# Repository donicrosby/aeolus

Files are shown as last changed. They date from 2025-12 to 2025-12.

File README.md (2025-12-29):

# Aeolus
A modular window extraction fan that uses common PC fans as the extraction component

## Setup
There are a few submodules that need to be pulled in this can be done by:

```bash
git clone --recurse-submodules https://github.com/donicrosby/aeolus.git
```

Or after already cloning the repo:

```bash
git clone ttps://github.com/donicrosby/aeolus.git
git submodule update --init --recursive
```

## Notes
This is a Kicad 9 project, ensure that you use that version when viewing

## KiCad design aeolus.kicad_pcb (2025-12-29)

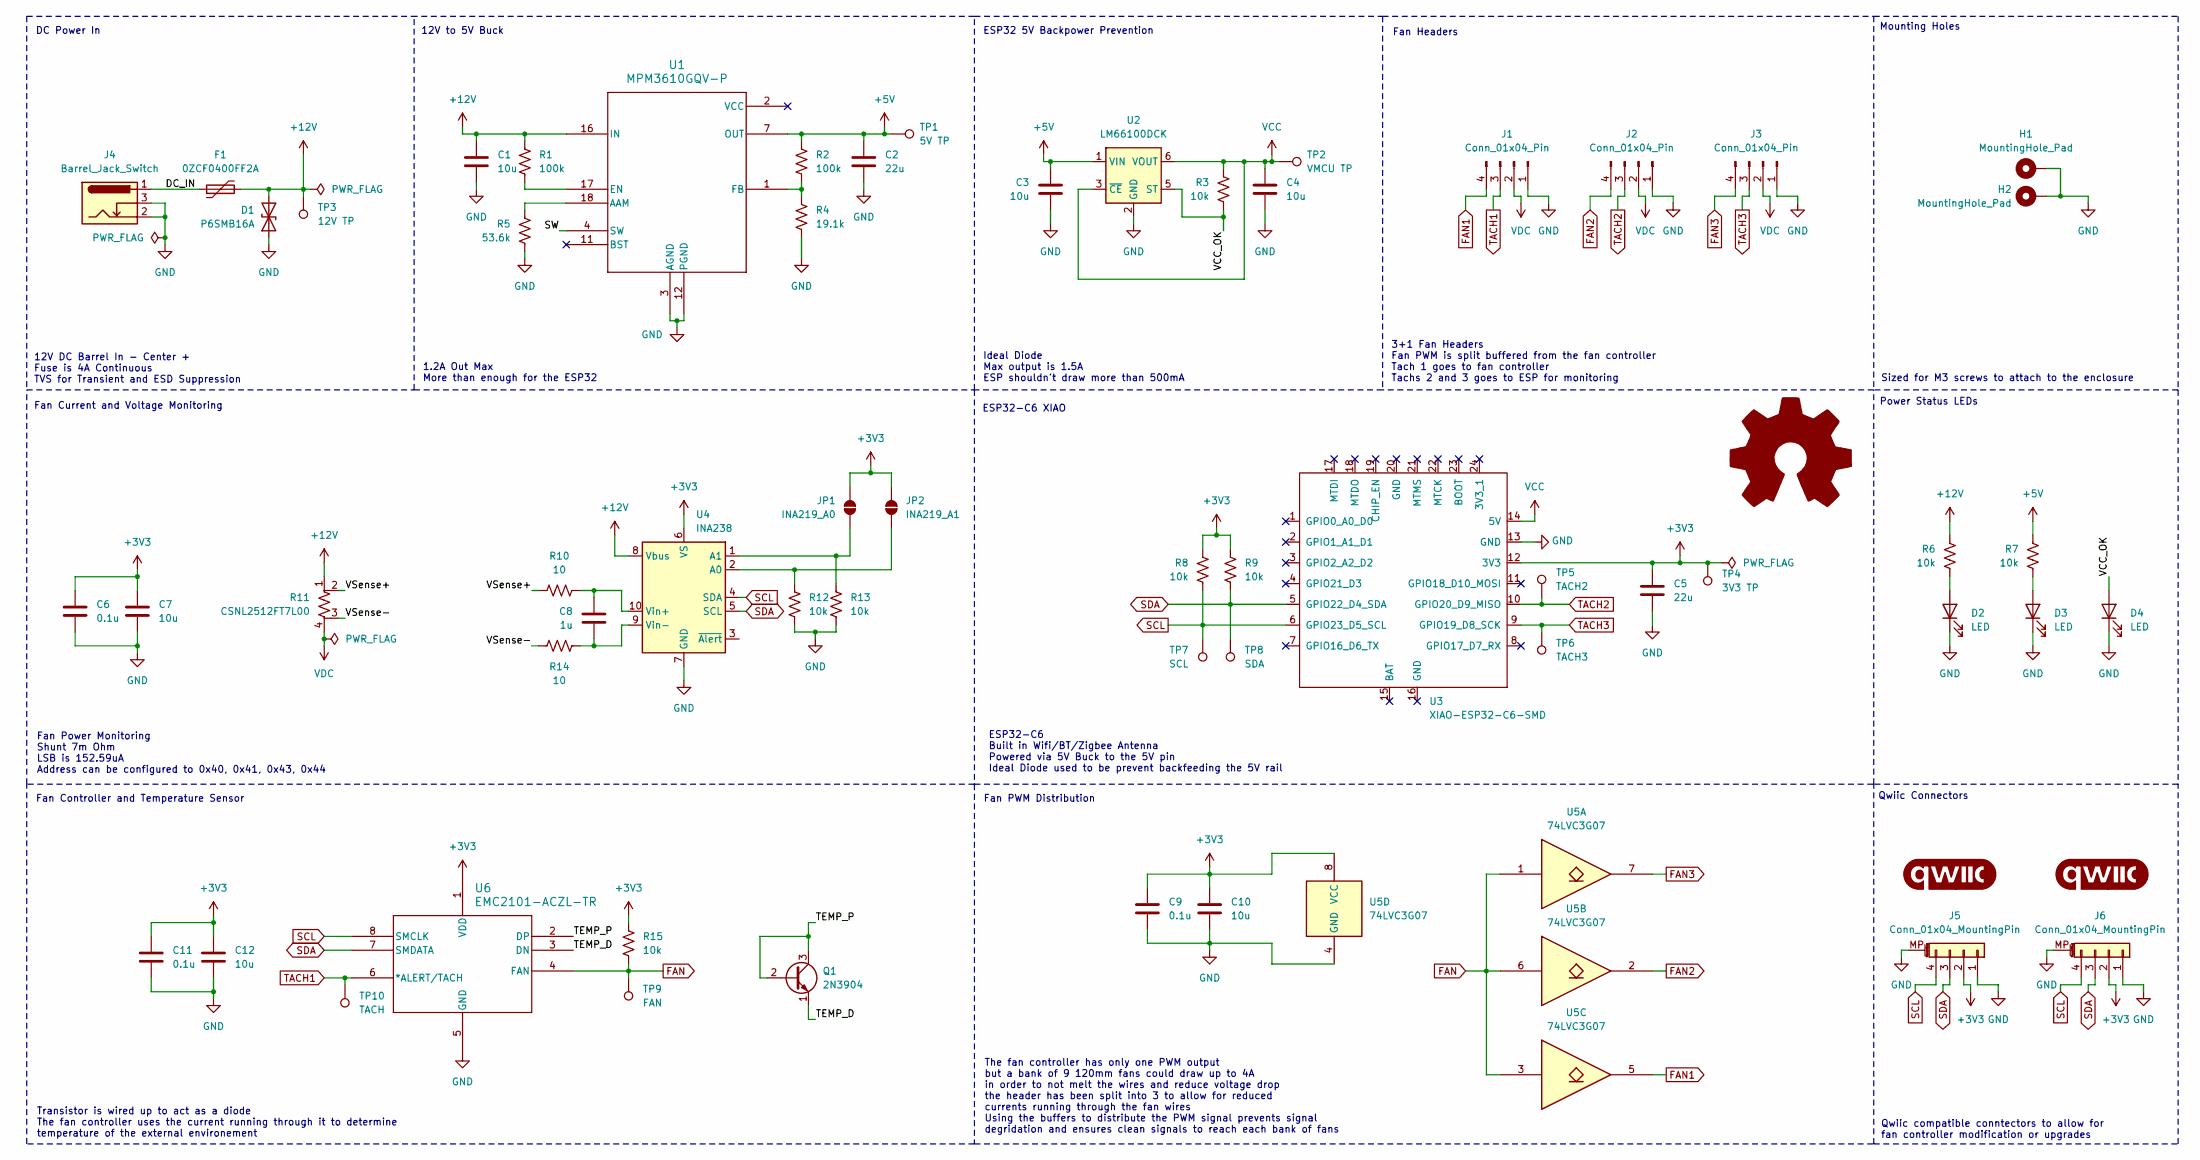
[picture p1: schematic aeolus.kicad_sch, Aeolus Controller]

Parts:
C1, C3, C4, C7, C10, C12: 10u; C_0805_2012Metric; MPN CL21A106KAYNNNE; LCSC C15850
C2, C5: 22u; C_0805_2012Metric; MPN CL21A226MAYNNNE; LCSC C602037
C6, C9, C11: 0.1u; C_0805_2012Metric; MPN CL21B104KBCNNNC; LCSC C5137467
C8: 1u; C_0805_2012Metric_Pad1.18x1.45mm_HandSolder; MPN CL21B105KBFNNNE; LCSC C5137467
D1: P6SMB16A; D_SMB; MPN P6SMB16A; LCSC C286252
D2: LED; LED_1206_3216Metric; MPN LTST-C150KSKT; LCSC C2985981
D3: LED; LED_1206_3216Metric; MPN LTST-C150KRKT; LCSC C2984265
D4: LED; LED_1206_3216Metric; MPN LTST-C150KGKT; LCSC C2984261
F1: 0ZCF0400FF2A; Fuse_2920_7451Metric; MPN 0ZCF0400FF2A
G1, G2: qwiic_Logo; qwiic_5.5mm
H1, H2: MountingHole_Pad; MountingHole_3.2mm_M3_Pad_Via
J1, J2, J3: Conn_01x04_Pin; FanPinHeader_1x04_P2.54mm_Vertical; MPN 470531000
J4: Barrel_Jack_Switch; BarrelJack_Wuerth_6941xx301002; MPN PJ-002AH
J5, J6: Conn_01x04_MountingPin; JST BM04B-SRSS-TB(LF)(SN)_4xP1.00mm; MPN BM04B-SRSS-TB(LF)(SN)
JP1: INA219_A0; SolderJumper-2_P1.3mm_Open_TrianglePad1.0x1.5mm
JP2: INA219_A1; SolderJumper-2_P1.3mm_Open_TrianglePad1.0x1.5mm
Q1: 2N3904; TO-92_Inline; MPN 2N3904
R1, R2: 100k; R_0805_2012Metric; MPN RC0805FR-07100KL; LCSC C96346
R3, R6, R7, R8, R9, R12, R13, R15: 10k; R_0805_2012Metric; MPN CRCW080510K0FKEAC; LCSC C84376
R4: 19.1k; R_0805_2012Metric; MPN RC0805FR-0719K1L; LCSC C2930175
R5: 53.6k; R_0805_2012Metric; MPN RC0805FR-0753K6L; LCSC C5153984
R10, R14: 10; R_0805_2012Metric_Pad1.20x1.40mm_HandSolder; MPN RM10J000CT; LCSC C17477
R11: CSNL2512FT7L00; Stackpole_Shunt_2512_Kelvin_7mOhm; MPN CMS-R050-1.0; LCSC C500733
TP1: 5V TP; TestPoint_Pad_D2.0mm
TP2: VMCU TP; TestPoint_Pad_D2.0mm
TP3: 12V TP; TestPoint_Pad_D2.0mm
TP4: 3V3 TP; TestPoint_Pad_D2.0mm
TP5: TACH2; TestPoint_Pad_D2.0mm
TP6: TACH3; TestPoint_Pad_D2.0mm
TP7: SCL; TestPoint_Pad_D2.0mm
TP8: SDA; TestPoint_Pad_D2.0mm
TP9: FAN; TestPoint_Pad_D2.0mm
TP10: TACH; TestPoint_Pad_D2.0mm
U1: MPM3610GQV-P; QFN3p0x5p0x1p6_MPM3610_MNP; MPN MPM3610GQV-P; LCSC C5183856
U2: LM66100DCK; SOT-363_SC-70-6; MPN LM66100DCKR; LCSC C2832141
U3: XIAO-ESP32-C6-SMD; XIAO-ESP32C6-SMD; MPN 113991254; LCSC C9900124963
U4: INA238; VSSOP-10_3x3mm_P0.5mm
U5: 74LVC3G07; SSOP-8_2.95x2.8mm_P0.65mm; MPN 74LVC3G07SS8-7; LCSC C2871847
U6: EMC2101-ACZL-TR; MSOP-8_3x3mm_P0.65mm; MPN EMC2101-ACZL-TR; LCSC C626967

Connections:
+3V3: C5.1, C6.1, C7.1, C9.1, C10.1, C11.1, C12.1, J5.2, J6.2, JP1.2 (B), JP2.2 (B), R8.1, R9.1, R15.1, TP4.1, U3.12 (3V3), U4.6 (VS), U5.8 (VCC), U6.1 (VDD)
+5V: C2.1, C3.1, R2.1, R7.1, TP1.1, U1.7 (OUT), U1.8 (OUT), U1.9 (OUT), U2.1 (VIN)
+12V: C1.1, D1.2 (A2), F1.2, R1.1, R6.1, R11.1, TP3.1, U1.16 (IN), U4.8 (Vbus)
/DC_IN: F1.1, J4.1
/SW: U1.4 (SW), U1.5 (SW), U1.6 (SW)
/TEMP_D: Q1.1 (E), U6.3 (DN)
/TEMP_P: Q1.2 (B), Q1.3 (C), U6.2 (DP)
/VCC_OK: D4.2 (A), R3.2, U2.5 (ST)
/VSense+: R10.1, R11.2
/VSense-: R11.3, R14.1
FAN: R15.2, TP9.1, U5.1, U5.3, U5.6, U6.4 (FAN)
FAN1: J1.4, U5.5
FAN2: J2.4, U5.2
FAN3: J3.4, U5.7
GND: C1.2, C2.2, C3.2, C4.2, C5.2, C6.2, C7.2, C9.2, C10.2, C11.2, C12.2, D1.1 (A1), D2.1 (K), D3.1 (K), D4.1 (K), H1.1, H2.1, J1.1, J2.1, J3.1, J4.2, J4.3, J5.1, J5.MP (MountPin), J6.1, J6.MP (MountPin), R4.2, R5.2, R12.2, R13.2, U1.3 (AGND), U1.12 (PGND), U1.13 (PGND), U1.14 (PGND), U2.2 (GND), U3.13 (GND), U4.7 (GND), U5.4 (GND), U6.5 (GND)
unnamed: D2.2 (A), R6.2
unnamed: D3.2 (A), R7.2
unnamed: JP1.1 (A), R13.1, U4.1 (A1)
unnamed: JP2.1 (A), R12.1, U4.2 (A0)
unnamed: R5.1, U1.18 (AAM)
unnamed: R1.2, U1.17 (EN)
unnamed: R2.2, R4.1, U1.1 (FB)
unnamed: C8.1, R10.2, U4.10 (Vin+)
unnamed: C8.2, R14.2, U4.9 (Vin-)
SCL: J5.4, J6.4, R8.2, TP7.1, U3.6 (GPIO23_D5_SCL), U4.4 (SDA), U6.8 (SMCLK)
SDA: J5.3, J6.3, R9.2, TP8.1, U3.5 (GPIO22_D4_SDA), U4.5 (SCL), U6.7 (SMDATA)
TACH1: J1.3, TP10.1, U6.6 (*ALERT/TACH)
TACH2: J2.3, TP5.1, U3.10 (GPIO20_D9_MISO)
TACH3: J3.3, TP6.1, U3.9 (GPIO19_D8_SCK)
VCC: C4.1, R3.1, TP2.1, U2.3 (~CE), U2.6 (VOUT), U3.14 (5V)
VDC: J1.2, J2.2, J3.2, R11.4

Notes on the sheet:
Fan Headers
Transistor is wired up to act as a diode The fan controller uses the current running through it to determine temperature of the external environement
ESP32 5V Backpower Prevention
12V to 5V Buck
3+1 Fan Headers Fan PWM is split buffered from the fan controller Tach 1 goes to fan controller Tachs 2 and 3 goes to ESP for monitoring
Ideal Diode Max output is 1.5A ESP shouldn't draw more than 500mA
Qwiic compatible conntectors to allow for fan controller modification or upgrades
The fan controller has only one PWM output but a bank of 9 120mm fans could draw up to 4A in order to not melt the wires and reduce voltage drop the header has been split into 3 to allow for reduced currents running through the fan wires Using the buffers to distribute the PWM signal prevents signa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
Fan Power Monitoring Shunt 7m Ohm LSB is 152.59uA Address can be configured to 0x40, 0x41, 0x43, 0x44
Mounting Holes
DC Power In
Sized for M3 screws to attach to the enclosure
1.2A Out Max More than enough for the ESP32
Fan Current and Voltage Monitoring
Fan PWM Distribution
12V DC Barrel In - Center + Fuse is 4A Continuous TVS for Transient and ESD Suppression
ESP32-C6 XIAO
Power Status LEDs
Fan Controller and Temperature Sensor
ESP32-C6 Built in Wifi/BT/Zigbee Antenna Powered via 5V Buck to the 5V pin Ideal Diode used to be prevent backfeeding the 5V rail
Qwiic Connectors

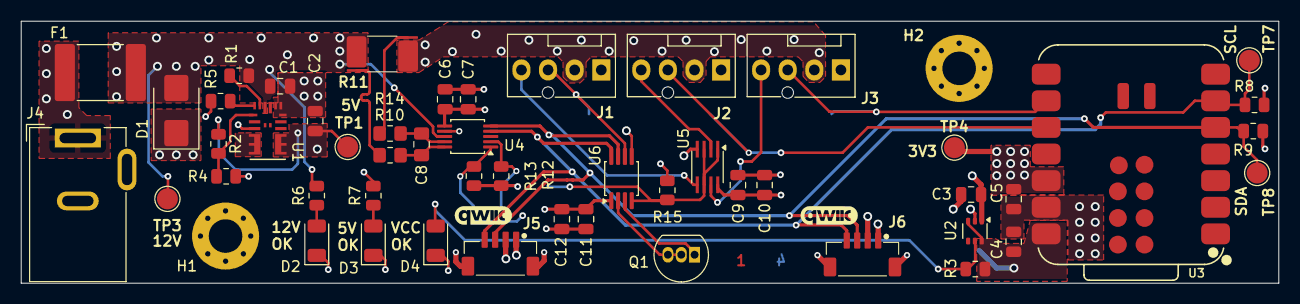
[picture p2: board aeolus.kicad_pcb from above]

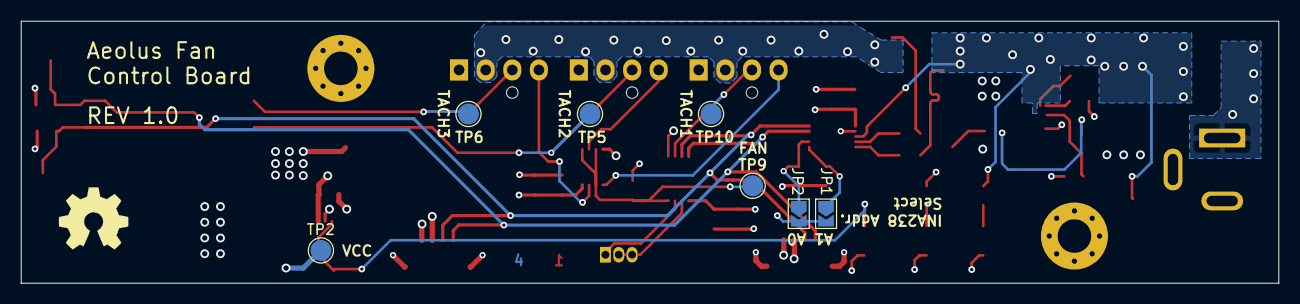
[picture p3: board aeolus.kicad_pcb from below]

Board: 4 copper layers, 120.0 x 25.0 mm, 61 parts (7 on the bottom side), 31 nets.

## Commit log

2025-12-01 feat: first pass at schematic
    [aeolus.kicad_pcb, aeolus.kicad_sch]
2025-12-01 More progress on PCB
    [aeolus.kicad_pcb]
2025-12-07 Inital pass at PCB
    [aeolus.kicad_pcb, aeolus.kicad_sch]
2025-12-08 Migrate to 4 layer board and beef up fan power distribution
    [aeolus.kicad_pcb, aeolus.kicad_sch]
2025-12-14 feat: update BOM for JLCPCB
    [aeolus.kicad_pcb]
2025-12-23 feat(bom): create production files
    [aeolus.kicad_pcb, aeolus.kicad_sch]
2025-12-24 fix(barrel jack): Fixed the fact that it was the wrong way around
    [aeolus.kicad_pcb, aeolus.kicad_sch]
2025-12-25 refactor: tweak design to be better for manufacturing
    [aeolus.kicad_pcb, aeolus.kicad_sch]
2025-12-28 refactor: use ina238 rather than ina219
    [aeolus.kicad_pcb, aeolus.kicad_sch]
2025-12-29 refactor: more tweaking of pcb
    [aeolus.kicad_pcb, aeolus.kicad_sch]
2025-12-29 feat: add qwiik connectors to board
    [aeolus.kicad_pcb, aeolus.kicad_sch]
2025-12-29 refactor: update Qwiic connector CAD model and footprint
    [aeolus.kicad_pcb, aeolus.kicad_sch]
2025-12-29 style: added OSHW and Qwiic Logos to PCB and Schematic
    [aeolus.kicad_pcb, aeolus.kicad_sch]

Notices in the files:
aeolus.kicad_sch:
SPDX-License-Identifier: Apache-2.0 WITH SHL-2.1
